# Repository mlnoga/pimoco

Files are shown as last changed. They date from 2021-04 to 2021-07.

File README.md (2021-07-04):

# pimoco

Telescope mount and focuser control with a Raspberry Pi 

Assembled PCB

## Motivation

Why do we need a separate device to control stepper motors attached to a telescope? Often times, a Raspberry Pi 4 running Ekos/Kstars/Indi will be attached to the telescope anyway, providing plenty of compute power. Modern stepper motor controllers like the Trinamic TMC5160 have an on-board motion controller which accepts position read, set target speed and go-to commands via SPI. The Raspberry Pi has two such interfaces for a total of five devices on its GPIO port.

This is 
* capable (1/256 microsteps, up to 1000x sidereal slewing, silent tracking, load-adaptive speed w/o step loss)
* robust (no Wifi, Bluetooth or USB connections to the mount as a source of error)
* beautiful (supports SkySafari on phones/tablets and game controllers via Ekos/Kstars/Indi) 
* inexpensive (no need for separate microcontrollers like OnStep or TeenAstro)
* manageable (no separate device firmware, only Indi drivers which Linux package managers can update)     

## [Wiki](../../wiki)

* [Hardware](../../wiki/Hardware)
* [Software](../../wiki/Software)
* [Results](../../wiki/Results)

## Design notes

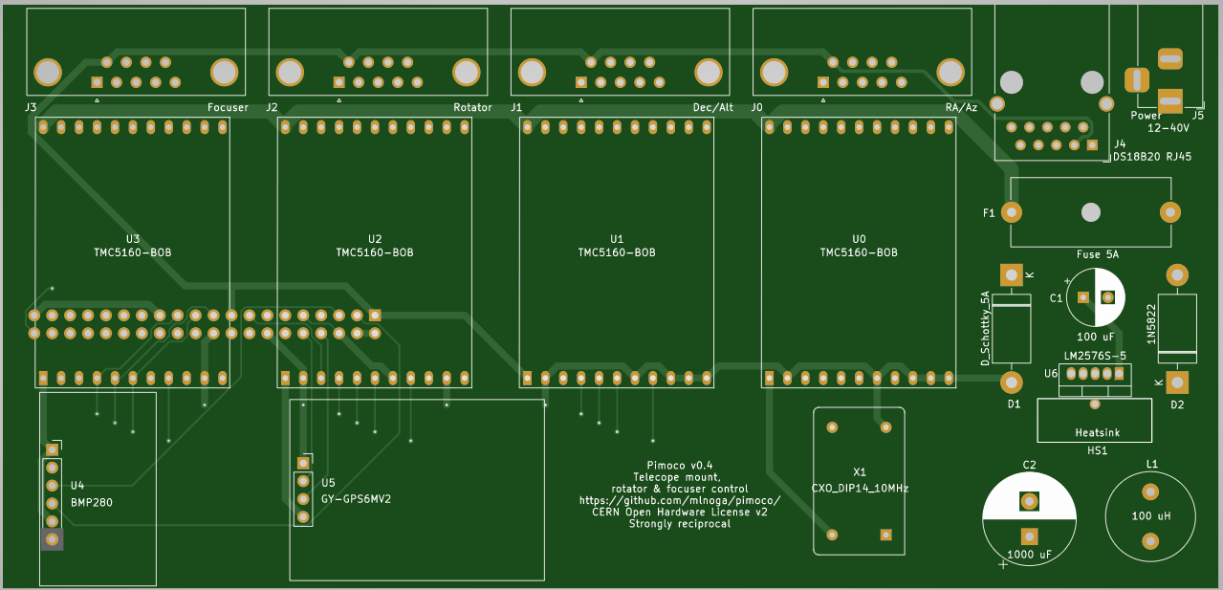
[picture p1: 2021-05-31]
hardware/images/top-v0.4.png

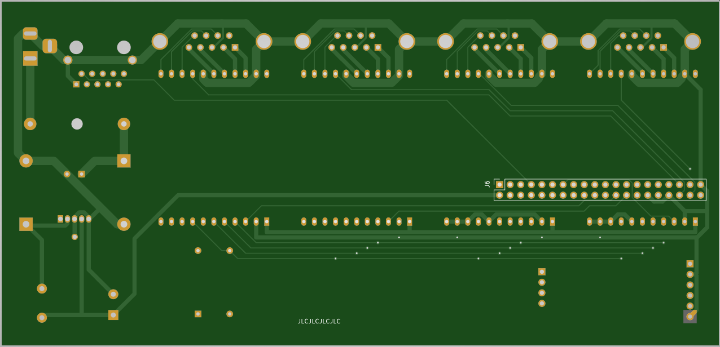
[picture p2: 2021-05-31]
hardware/images/bottom-v0.4.png

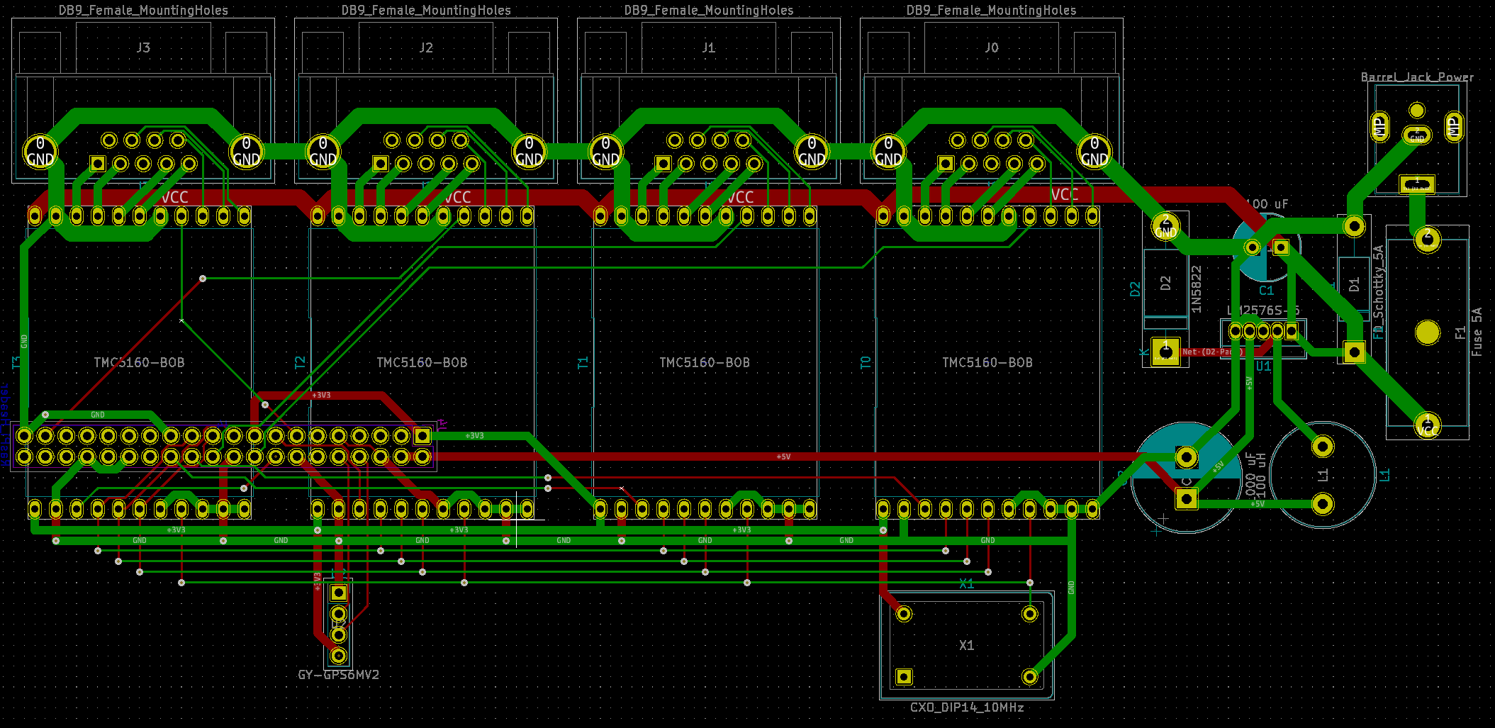
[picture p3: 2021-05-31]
hardware/images/platinenlayout.png

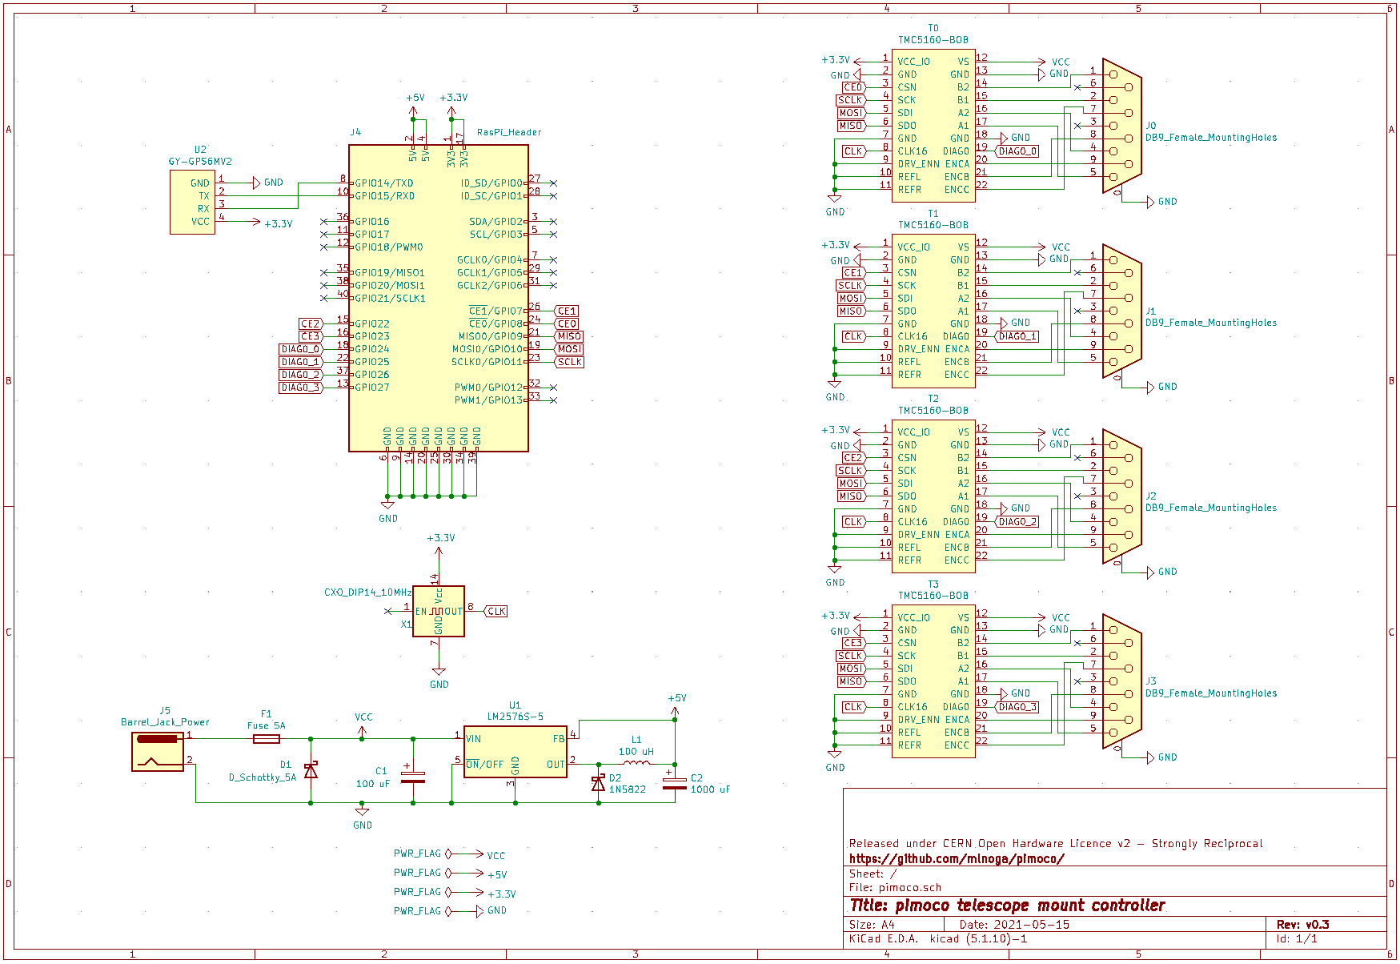
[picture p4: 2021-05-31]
hardware/images/schaltplan.png

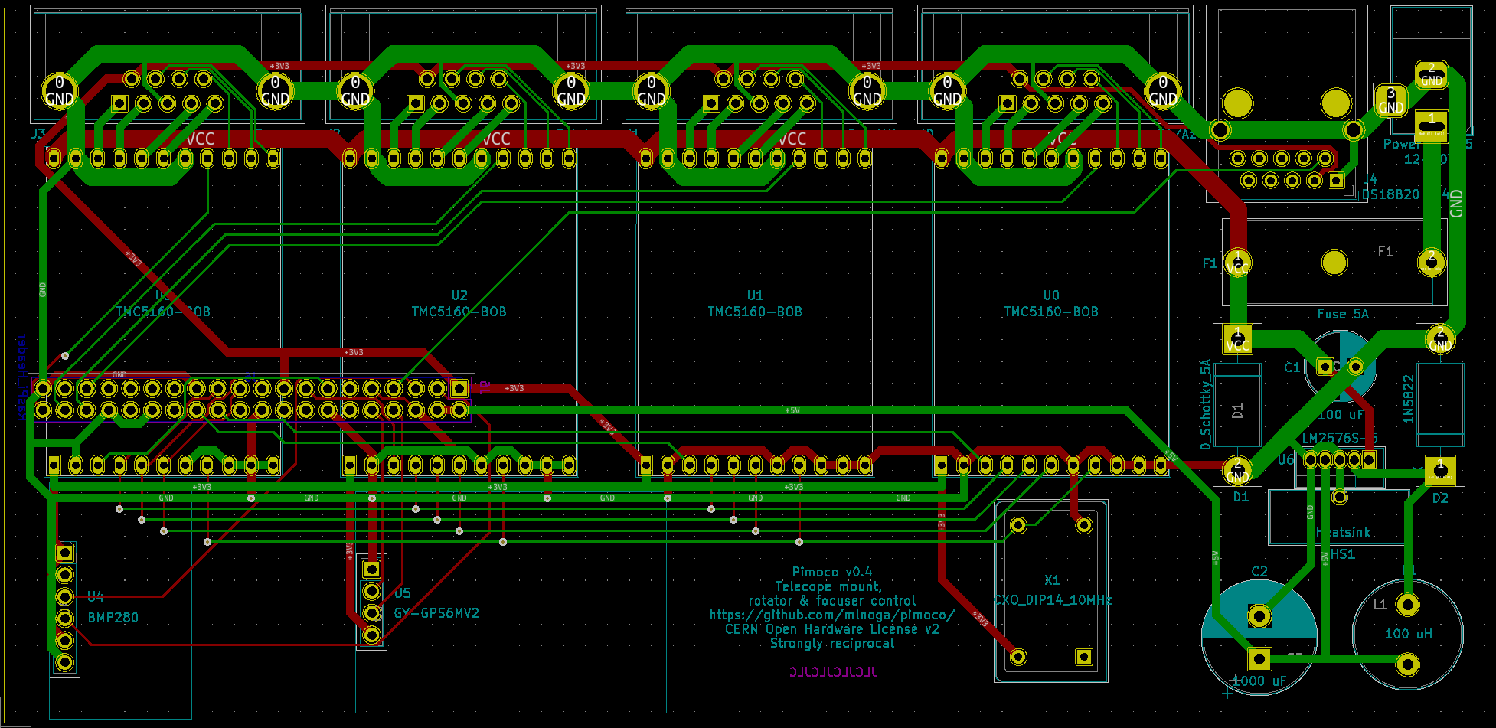
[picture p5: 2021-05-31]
hardware/images/layout-v0.4.png

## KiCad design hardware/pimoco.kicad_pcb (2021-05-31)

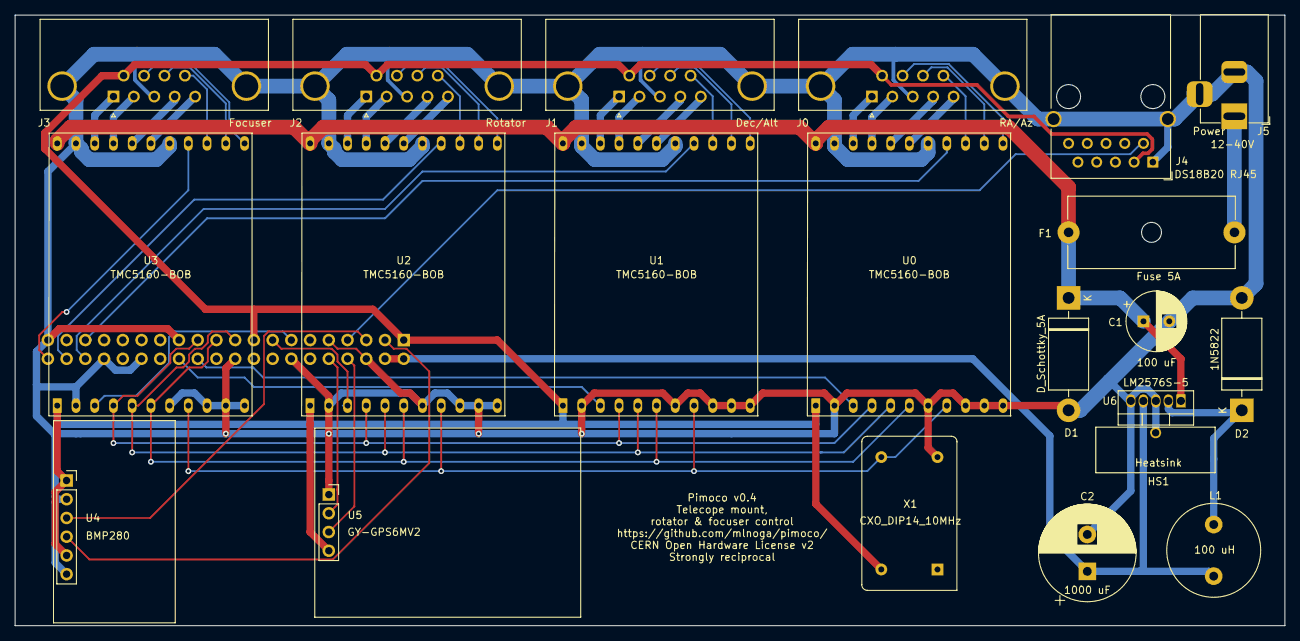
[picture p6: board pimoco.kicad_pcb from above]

Board: 2 copper layers, 172.2 x 82.8 mm, 22 parts (1 on the bottom side), 51 nets.

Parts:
C1: 100 uF; CP_Radial_D8.0mm_P3.50mm
C2: 1000 uF; CP_Radial_D13.0mm_P5.00mm
D1: D_Schottky_5A; D_DO-201AD_P15.24mm_Horizontal
D2: 1N5822; D_DO-201AD_P15.24mm_Horizontal
F1: Fuse 5A; Fuseholder_Cylinder-5x20mm_Schurter_0031_8201_Horizontal_Op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
HS1: Heatsink; Heatsink_TO-220_vertical
J0: RA/Az; DSUB-9_Female_Horizontal_P2.77x2.84mm_EdgePinOffset7.70mm_H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
J1: Dec/Alt; DSUB-9_Female_Horizontal_P2.77x2.84mm_EdgePinOffset7.70mm_H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
J2: Rotator; DSUB-9_Female_Horizontal_P2.77x2.84mm_EdgePinOffset7.70mm_H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
J3: Focuser; DSUB-9_Female_Horizontal_P2.77x2.84mm_EdgePinOffset7.70mm_H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
J4: DS18B20 RJ45; RJ45_Wuerth_7499111446_Horizontal-modified
J5: Power; BarrelJack_Horizontal
J6: RasPi_Header; PinSocket_2x20_P2.54mm_Vertical
L1: 100 uH; L_Radial_D12.5mm_P7.00mm_Fastron_09HCP
U0, U1, U2, U3: TMC5160-BOB; TMC5160-BOB2
U4: BMP280; BMP280-Breakout
U5: GY-GPS6MV2
U6: LM2576S-5; TO-220-5_Vertical
X1: CXO_DIP14_10MHz; Oscillator_DIP-14

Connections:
+3V3: J0.6, J1.6, J2.6, J3.6, J4.3, J6.1, J6.17, U0.1, U1.1, U2.1, U3.1, U4.1, U4.5, U5.4, X1.14
+5V: C2.1, J6.2, J6.4, L1.2, U6.4
CE0: J6.24, U0.3
CE1: J6.26, U1.3
CE2: J6.15, U2.3
CE3: J6.13, U3.3
CLK: U0.8, U1.8, U2.8, U3.8, X1.8
DIAG0_0: J6.35, U0.19
DIAG0_1: J6.36, U1.19
DIAG0_2: J6.38, U2.19
DIAG0_3: J6.40, U3.19
GND: C1.2, C2.2, D1.2, D2.2, HS1.1, J0.0, J0.3, J1.0, J1.3, J2.0, J2.3, J3.0, J3.3, J4.1, J4.SH, J5.2, J5.3, J6.6, J6.9, J6.14, J6.20, J6.25, J6.30, J6.34, J6.39, U0.2, U0.7, U0.9, U0.10, U0.11, U0.13, U0.18, U1.2, U1.7, U1.9, U1.10, U1.11, U1.13, U1.18, U2.2, U2.7, U2.9, U2.10, U2.11, U2.13, U2.18, U3.2, U3.7, U3.9, U3.10, U3.11, U3.13, U3.18, U4.2, U4.6, U5.1, U6.3, U6.5, X1.7
MISO: J6.21, U0.6, U1.6, U2.6, U3.6
MOSI: J6.19, U0.5, U1.5, U2.5, U3.5
unnamed: D2.1, L1.1, U6.2
unnamed: F1.2, J5.1
unnamed: J0.1, U0.14
unnamed: J0.2, U0.15
unnamed: J0.4, U0.16
unnamed: J0.5, U0.17
unnamed: J0.7, U0.22
unnamed: J0.8, U0.21
unnamed: J0.9, U0.20
unnamed: J1.1, U1.14
unnamed: J1.2, U1.15
unnamed: J1.4, U1.16
unnamed: J1.5, U1.17
unnamed: J1.7, U1.22
unnamed: J1.8, U1.21
unnamed: J1.9, U1.20
unnamed: J2.1, U2.14
unnamed: J2.2, U2.15
unnamed: J2.4, U2.16
unnamed: J2.5, U2.17
unnamed: J2.7, U2.22
unnamed: J2.8, U2.21
unnamed: J2.9, U2.20
unnamed: J3.1, U3.14
unnamed: J3.2, U3.15
unnamed: J3.4, U3.16
unnamed: J3.5, U3.17
unnamed: J3.7, U3.22
unnamed: J3.8, U3.21
unnamed: J3.9, U3.20
unnamed: J4.2, J6.7
unnamed: J6.3, U4.4
unnamed: J6.5, U4.3
unnamed: J6.8, U5.3
unnamed: J6.10, U5.2
SCLK: J6.23, U0.4, U1.4, U2.4, U3.4
VCC: C1.1, D1.1, F1.1, U0.12, U1.12, U2.12, U3.12, U6.1

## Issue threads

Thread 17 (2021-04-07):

Enhance motor control with SpreadChop/FullStep/StallGuard etc.

mlnoga, 2021-04-07:

Closed 2021-04-28.

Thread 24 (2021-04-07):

Add support for meridian flip to mount

mlnoga, 2021-04-07:

Closed 2021-05-09.

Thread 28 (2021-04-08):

Add 5V 3A voltage regulator to breadboard to power the pi w/o separate PSU

mlnoga, 2021-04-08:

mlnoga, 2021-04-28:
E.g. the [LM2576](https://www.ti.com/lit/ds/symlink/lm2576.pdf)

mlnoga, 2021-05-05:
Successful. See [wiki](https://github.com/mlnoga/pimoco/wiki/Hardware)

Closed 2021-05-05.

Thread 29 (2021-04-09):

Set gpclk0 with wiringPi to remove need for an /etc/rc.local entry

mlnoga, 2021-04-09:

mlnoga, 2021-04-24:
GPCLK0 rates are different on Pi4 than Pi3 by a factor of approx. 3x. Exact base clocks are undocumented in the Broadcom CPU reference. Abandoning this approach and moving to external 10 MHz crystal oscillator.

Closed 2021-04-24.

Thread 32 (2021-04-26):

Gotos dont consistently signal completion.

mlnoga, 2021-04-26:
Gotos dont consistently signal completion.

mlnoga, 2021-05-12:
The underlying issue seems to be that the TMC5160 really does need SPI mode 3, which is broken on RPI SPI1 and SPI2.

So far I've used [Raspberry Pi SPI ](https://www.raspberrypi.org/documentation/hardware/raspberrypi/spi/README.md) port 1, because it supports three CS lines for the three steppers. This keeps MISO/MOSI/Clock wiring to a minimum. I've had initial success, but not full stability, with mode 0. Here's the `dmesg` kernel log entry when trying to set mode 3:

```
spidev spi1.0: setup: unsupported mode bits 1
```

So the Broadcom chipset for the two so-called "mini" SPI ports 1 and 2 appears to be broken. According to these sources, it only supports modes 0 and 2:

* [Stackexchange](https://raspberrypi.stackexchange.com/questions/106456/cant-set-modes-1-and-3-in-auxillary-spi1)
* [Raspberry Pi Forum](https://www.raspberrypi.org/forums/viewtopic.php?p=1071641)

The fix appears to be to use the full SPI port 0 with two CS lines, and another of the new SPI ports 3-6 available on RPi4. With header pin numbers, available ports are:

| Line    | SPI0  | SPI3 | SPI4 | SPI 5 | SPI6 |
|--------|-------|------|------|-------|------|
| MOSI  |   19   |    3   |  31  |     8   |   38   |
| MISO  |    21  |   28  |  29  |   33   |   35   |
| SCLK  |     23  |     5  |  26  |   10   |   40   |
| CE0    |     24  |   27  |  07  |   32   |   12   |
| CE1    |     26  |   18  |  22  |   37   |   13   |

So hardware change required, and restriction to RPI4 and above when needing three or more SPI ports.

mlnoga, 2021-05-12:
Looks like SPI0 and SPI3 are the way to go.

[Device tree README](https://github.com/raspberrypi/firmware/blob/master/boot/overlays/README)

mlnoga, 2021-05-24:
SPI0 with CS0, CS1, CS2, CS3 is the way to go.

mlnoga, 2021-05-25:
Another issue is HA endlessly chasing the target position at low speeds due to target resets

Closed 2021-05-25.

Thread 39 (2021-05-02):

When mount limits disable tracking, it doesn't automatically reenable once the mount is back within limits

mlnoga, 2021-05-02:

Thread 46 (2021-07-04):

Telescope driver crashes after motor initialization with new PCB

mlnoga, 2021-07-04:
Logfile

```
[2021-07-04T12:06:55.642 CEST DEBG ][                org.kde.kstars] - Daylight Saving Time active
[2021-07-04T12:06:55.643 CEST DEBG ][                org.kde.kstars] - Next Daylight Savings Time change (Local Time):  "Sun Oct 31 00:59:59 2021 GMT"
[2021-07-04T12:06:55.643 CEST DEBG ][                org.kde.kstars] - Next Daylight Savings Time change (UTC):  "Sat Oct 30 22:59:59 2021 GMT"
[2021-07-04T12:06:55.643 CEST DEBG ][                org.kde.kstars] - Starting the timer
[2021-07-04T12:06:55.962 CEST DEBG ][           org.kde.kstars.ekos] - Resetting Ekos Manager...
[2021-07-04T12:06:56.032 CEST INFO ][           org.kde.kstars.ekos] - "Starting INDI services..."
[2021-07-04T12:06:56.033 CEST DEBG ][           org.kde.kstars.indi] - INDI: Starting local drivers...
[2021-07-04T12:06:56.034 CEST DEBG ][           org.kde.kstars.indi] - Starting INDI Server:  ("-v", "-p", "7624", "-m", "1024", "-r", "0", "-f", "/tmp/indififo039d8cfc") -f "/tmp/indififo039d8cfc"
[2021-07-04T12:06:56.051 CEST DEBG ][           org.kde.kstars.indi] - INDI Server Started?  true
[2021-07-04T12:06:56.052 CEST DEBG ][           org.kde.kstars.indi] - INDI: INDI Server started locally on port  7624
[2021-07-04T12:06:56.052 CEST DEBG ][           org.kde.kstars.indi] - Starting INDI Driver  "indi_pimoco_mount"
[2021-07-04T12:06:56.053 CEST DEBG ][           org.kde.kstars.indi] - Starting INDI Driver  "indi_asi_ccd"
[2021-07-04T12:06:56.053 CEST DEBG ][           org.kde.kstars.indi] - Starting INDI Driver  "indi_asi_wheel"
[2021-07-04T12:06:56.053 CEST DEBG ][           org.kde.kstars.indi] - Starting INDI Driver  "indi_pimoco_focuser"
[2021-07-04T12:06:56.054 CEST DEBG ][           org.kde.kstars.indi] - Starting INDI Driver  "indi_joystick"
[2021-07-04T12:06:56.054 CEST DEBG ][           org.kde.kstars.indi] - Starting INDI Driver  "indi_skysafari"
[2021-07-04T12:06:56.054 CEST DEBG ][           org.kde.kstars.indi] - Adding managed driver "Pimoco mount"
[2021-07-04T12:06:56.054 CEST DEBG ][           org.kde.kstars.indi] - Adding managed driver "ZWO CCD"
[2021-07-04T12:06:56.054 CEST DEBG ][           org.kde.kstars.indi] - Adding managed driver "ASI EFW"
[2021-07-04T12:06:56.055 CEST DEBG ][           org.kde.kstars.indi] - Adding managed driver "Pimoco focuser"
[2021-07-04T12:06:56.055 CEST DEBG ][           org.kde.kstars.indi] - Adding managed driver "Joystick"
[2021-07-04T12:06:56.055 CEST DEBG ][           org.kde.kstars.indi] - Adding managed driver "SkySafari"
[2021-07-04T12:06:56.057 CEST DEBG ][           org.kde.kstars.indi] - INDIListener: Adding a new client manager to INDI listener..
[2021-07-04T12:06:56.057 CEST DEBG ][           org.kde.kstars.indi] - INDI: Connecting to local INDI server on port  7624  ...
[2021-07-04T12:06:56.059 CEST DEBG ][           org.kde.kstars.indi] - Connection to INDI server is successful
[2021-07-04T12:06:56.060 CEST INFO ][           org.kde.kstars.ekos] - "INDI services started on port 7624."
[2021-07-04T12:06:56.072 CEST DEBG ][           org.kde.kstars.indi] - INDI server connected.
[2021-07-04T12:06:56.135 CEST DEBG ][           org.kde.kstars.indi] - Received new device Pimoco focuser
[2021-07-04T12:06:56.157 CEST DEBG ][           org.kde.kstars.indi] - INDI Server:  "2021-07-04T10:06:56: startup: /usr/bin/indiserver -v -p 7624 -m 1024 -r 0 -f /tmp/indififo039d8cfc "
[2021-07-04T12:06:56.158 CEST DEBG ][           org.kde.kstars.indi] - INDI Server:  "2021-07-04T10:06:56: listening to port 7624 on fd 3"
[2021-07-04T12:06:56.158 CEST DEBG ][           org.kde.kstars.indi] - INDI Server:  "FIFO: start indi_pimoco_mount -n \"Pimoco mount\""
[2021-07-04T12:06:56.158 CEST DEBG ][           org.kde.kstars.indi] - INDI Server:  "With name: Pimoco mount"
[2021-07-04T12:06:56.158 CEST DEBG ][           org.kde.kstars.indi] - INDI Server:  "FIFO: Starting driver indi_pimoco_mount"
[2021-07-04T12:06:56.159 CEST DEBG ][           org.kde.kstars.indi] - INDI Server:  "2021-07-04T10:06:56: Driver indi_pimoco_mount: pid=2469 rfd=4 wfd=7 efd=8"
[2021-07-04T12:06:56.159 CEST DEBG ][           org.kde.kstars.indi] - INDI Server:  "FIFO: start indi_asi_ccd"
[2021-07-04T12:06:56.159 CEST DEBG ][           org.kde.kstars.indi] - INDI Server:  "FIFO: Starting driver indi_asi_ccd"
[2021-07-04T12:06:56.159 CEST DEBG ][           org.kde.kstars.indi] - INDI Server:  "2021-07-04T10:06:56: Driver indi_asi_ccd: pid=2470 rfd=5 wfd=10 efd=11"
[2021-07-04T12:06:56.159 CEST DEBG ][           org.kde.kstars.indi] - INDI Server:  "FIFO: start indi_asi_wheel"
[2021-07-04T12:06:56.160 CEST DEBG ][           org.kde.kstars.indi] - INDI Server:  "FIFO: Starting driver indi_asi_wheel"
[2021-07-04T12:06:56.160 CEST DEBG ][           org.kde.kstars.indi] - INDI Server:  "2021-07-04T10:06:56: Driver indi_asi_wheel: pid=2471 rfd=6 wfd=15 efd=16"
[2021-07-04T12:06:56.160 CEST DEBG ][           org.kde.kstars.indi] - INDI Server:  "FIFO: start indi_pimoco_focuser -n \"Pimoco focuser\""
[2021-07-04T12:06:56.160 CEST DEBG ][           org.kde.kstars.indi] - INDI Server:  "With name: Pimoco focuser"
[2021-07-04T12:06:56.160 CEST DEBG ][           org.kde.kstars.indi] - INDI Server:  "FIFO: Starting driver indi_pimoco_focuser"
[2021-07-04T12:06:56.161 CEST DEBG ][           org.kde.kstars.indi] - INDI Server:  "2021-07-04T10:06:56: Driver indi_pimoco_focuser: pid=2472 rfd=9 wfd=18 efd=19"
[2021-07-04T12:06:56.161 CEST DEBG ][           org.kde.kstars.indi] - INDI Server:  "FIFO: start indi_joystick -n \"Joystick\""
[2021-07-04T12:06:56.161 CEST DEBG ][           org.kde.kstars.indi] - INDI Server:  "With name: Joystick"
[2021-07-04T12:06:56.161 CEST DEBG ][           org.kde.kstars.indi] - INDI Server:  "FIFO: Starting driver indi_joystick"
[2021-07-04T12:06:56.161 CEST DEBG ][           org.kde.kstars.indi] - INDI Server:  "2021-07-04T10:06:56: Driver indi_joystick: pid=2473 rfd=12 wfd=21 efd=22"
[2021-07-04T12:06:56.162 CEST DEBG ][           org.kde.kstars.indi] - INDI Server:  "FIFO: start indi_skysafari -n \"SkySafari\""
[2021-07-04T12:06:56.162 CEST DEBG ][           org.kde.kstars.indi] - INDI Server:  "With name: SkySafari"
[2021-07-04T12:06:56.162 CEST DEBG ][           org.kde.kstars.indi] - INDI Server:  "FIFO: Starting driver indi_skysafari"
[2021-07-04T12:06:56.162 CEST DEBG ][           org.kde.kstars.indi] - INDI Server:  "2021-07-04T10:06:56: Driver indi_skysafari: pid=2474 rfd=17 wfd=24 efd=25"
[2021-07-04T12:06:56.162 CEST DEBG ][           org.kde.kstars.indi] - INDI Server:  "2021-07-04T10:06:56: Client 20: new arrival from 127.0.0.1:41234 - welcome!"
[2021-07-04T12:06:56.163 CEST DEBG ][           org.kde.kstars.indi] - INDI Server:  "2021-07-04T10:06:56: Driver indi_pimoco_mount: snooping on GPS Simulator.GEOGRAPHIC_COORD"
[2021-07-04T12:06:56.163 CEST DEBG ][           org.kde.kstars.indi] - INDI Server:  "2021-07-04T10:06:56: Driver indi_pimoco_mount: snooping on GPS Simulator.TIME_UTC"
[2021-07-04T12:06:56.163 CEST DEBG ][           org.kde.kstars.indi] - INDI Server:  "2021-07-04T10:06:56: Driver indi_pimoco_mount: snooping on Dome Simulator.DOME_PARK"
[2021-07-04T12:06:56.163 CEST DEBG ][           org.kde.kstars.indi] - INDI Server:  "2021-07-04T10:06:56: Driver indi_pimoco_mount: snooping on Dome Simulator.DOME_SHUTTER"
[2021-07-04T12:06:56.164 CEST DEBG ][           org.kde.kstars.indi] - INDI Server:  "2021-07-04T10:06:56: Driver indi_asi_wheel: Searching for HID Device VID: 0x3c3 PID: 0x1f01"
[2021-07-04T12:06:56.164 CEST DEBG ][           org.kde.kstars.indi] - INDI Server:  ""
[2021-07-04T12:06:56.208 CEST DEBG ][           org.kde.kstars.indi] - INDIListener: New device "Pimoco focuser"
[2021-07-04T12:06:56.208 CEST INFO ][           org.kde.kstars.ekos] - Ekos received a new device:  "Pimoco focuser"
[2021-07-04T12:06:56.214 CEST DEBG ][           org.kde.kstars.indi] - Received new device Pimoco mount
[2021-07-04T12:06:56.215 CEST DEBG ][           org.kde.kstars.indi] - INDI Server:  "2021-07-04T10:06:56: Driver indi_asi_wheel: Searching for HID Device VID: 0x3c3 PID: 0x1f02"
[2021-07-04T12:06:56.216 CEST DEBG ][           org.kde.kstars.indi] - INDI Server:  "2021-07-04T10:06:56: Driver indi_asi_wheel: No ASI EFW detected.Searching for HID Device VID: 0x3c3 PID: 0x1f01"
[2021-07-04T12:06:56.216 CEST DEBG ][           org.kde.kstars.indi] - INDI Server:  "2021-07-04T10:06:56: Driver indi_asi_wheel: Searching for HID Device VID: 0x3c3 PID: 0x1f02"
[2021-07-04T12:06:56.217 CEST DEBG ][           org.kde.kstars.indi] - INDI Server:  ""
[2021-07-04T12:06:56.358 CEST DEBG ][           org.kde.kstars.indi] - INDIListener: New device "Pimoco mount"
[2021-07-04T12:06:56.359 CEST INFO ][           org.kde.kstars.ekos] - Ekos received a new device:  "Pimoco mount"
[2021-07-04T12:06:56.366 CEST DEBG ][           org.kde.kstars.indi] - Received new device SkySafari
[2021-07-04T12:06:56.501 CEST DEBG ][           org.kde.kstars.indi] - INDI Server:  "2021-07-04T10:06:56: Client 23: new arrival from 127.0.0.1:41236 - welcome!"
[2021-07-04T12:06:56.502 CEST DEBG ][           org.kde.kstars.indi] - INDI Server:  "2021-07-04T10:06:56: Driver indi_asi_wheel: No ASI EFW detected.Searching for HID Device VID: 0x3c3 PID: 0x1f01"
[2021-07-04T12:06:56.503 CEST DEBG ][           org.kde.kstars.indi] - INDI Server:  "2021-07-04T10:06:56: Driver indi_asi_wheel: Searching for HID Device VID: 0x3c3 PID: 0x1f02"
[2021-07-04T12:06:56.503 CEST DEBG ][           org.kde.kstars.indi] - INDI Server:  ""
[2021-07-04T12:06:56.510 CEST DEBG ][           org.kde.kstars.indi] - < Pimoco mount >: < CONNECTION >
[2021-07-04T12:06:56.513 CEST DEBG ][           org.kde.kstars.indi] - < Pimoco mount >: < DRIVER_INFO >
[2021-07-04T12:06:56.521 CEST DEBG ][           org.kde.kstars.indi] - < Pimoco mount >: < POLLING_PERIOD >
[2021-07-04T12:06:56.524 CEST DEBG ][           org.kde.kstars.indi] - < Pimoco mount >: < DEBUG >
[2021-07-04T12:06:56.527 CEST DEBG ][           org.kde.kstars.indi] - < Pimoco mount >: < CONFIG_PROCESS >
[2021-07-04T12:06:56.529 CEST DEBG ][           org.kde.kstars.indi] - < Pimoco focuser >: < CONNECTION >
[2021-07-04T12:06:56.533 CEST DEBG ][           org.kde.kstars.indi] - < Pimoco focuser >: < DRIVER_INFO >
[2021-07-04T12:06:56.541 CEST DEBG ][           org.kde.kstars.indi] - < Pimoco focuser >: < DEBUG >
[2021-07-04T12:06:56.544 CEST DEBG ][           org.kde.kstars.indi] - < Pimoco focuser >: < POLLING_PERIOD >
[2021-07-04T12:06:56.551 CEST DEBG ][           org.kde.kstars.indi] - < Pimoco focuser >: < CONFIG_PROCESS >
[2021-07-04T12:06:56.555 CEST INFO ][           org.kde.kstars.indi] - Pimoco focuser :  "[INFO] Debug is enabled. "
[2021-07-04T12:06:56.555 CEST DEBG ][           org.kde.kstars.indi] - < Pimoco focuser >: < DEBUG_LEVEL >
[2021-07-04T12:06:56.557 CEST DEBG ][           org.kde.kstars.indi] - < Pimoco focuser >: < LOGGING_LEVEL >
[2021-07-04T12:06:56.559 CEST DEBG ][           org.kde.kstars.indi] - < Pimoco focuser >: < LOG_OUTPUT >
[2021-07-04T12:06:56.561 CEST DEBG ][           org.kde.kstars.indi] - Pimoco focuser : "[DEBUG] Toggle Debug Level -- Driver Debug "
[2021-07-04T12:06:56.561 CEST DEBG ][           org.kde.kstars.indi] - Pimoco focuser : "[DEBUG] Toggle Logging Level -- Messages "
[2021-07-04T12:06:56.571 CEST DEBG ][           org.kde.kstars.indi] - INDIListener: New device "SkySafari"
[2021-07-04T12:06:56.572 CEST INFO ][           org.kde.kstars.ekos] - Ekos received a new device:  "SkySafari"
[2021-07-04T12:06:56.573 CEST DEBG ][           org.kde.kstars.indi] - Received new device Joystick
[2021-07-04T12:06:56.599 CEST DEBG ][           org.kde.kstars.indi] - < SkySafari >: < CONNECTION >
[2021-07-04T12:06:56.604 CEST DEBG ][           org.kde.kstars.indi] - < SkySafari >: < DRIVER_INFO >
[2021-07-04T12:06:56.619 CEST DEBG ][           org.kde.kstars.indi] - < SkySafari >: < DEBUG >
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

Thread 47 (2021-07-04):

Fix minor hardware issues in PCB v0.4

mlnoga, 2021-07-04:
- Make drill hole for heat sink 0.3mm wider
- Move GPS connector pin left towards BMP sensor to leave more room for the GPS antenna
- Move RPi connector header down away from connector edge to make connectors flush with the connectors on the RPI itself

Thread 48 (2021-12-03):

I think the .lib file is missing from the hardware folder

skieast, 2021-12-03:
I was trying to look at the schematic in KiCad and the symbols aren't defined.
Thanks

Closed 2021-12-04.

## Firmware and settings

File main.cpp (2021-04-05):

/*
    PiMoCo: Raspberry Pi Telescope Mount and Focuser Control
    Copyright (C) 2021 Markus Noga

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
    You should have received a copy of the GNU General Public License
    along with this program.  If not, see <https://www.gnu.org/licenses/>.
*/


#include <stdio.h>
#include <stdarg.h>
#include <stdlib.h>
#include <locale.h> // for thousands separator
#include <unistd.h> // for sleep
#include <libindi/indifocuser.h>

#include "pimoco_stepper.h"

// Unused dummies for Indi functions to avoid linker errors
//
extern "C" {

void ISGetProperties(const char *dev) {}

void ISNewBLOB(const char *dev, const char *name, int sizes[], int blobsizes[], char *blobs[], char *formats[], char *names[], int n) {}

void ISNewNumber(const char *dev, const char *name, double values[], char *names[], int n) {}

void ISNewSwitch(const char *dev, const char *name, ISState *states, char *names[], int n) {}

void ISNewText(const char *dev, const char *name, char *texts[], char *names[], int n) {}

void ISSnoopDevice(XMLEle *root) {}

} // extern "C"


void panicf(const char *fmt, ...) {
	va_list argp;
	va_start(argp, fmt);
	vfprintf(stdout, fmt, argp);
	exit(-1);
}

void getAndPrintState(Stepper *stepper) {
	int32_t pos, speed;
	if(!stepper->getPosition(&pos) || !stepper->getSpeed(&speed))
		panicf("Error getting position and speed\n");

	printf("Current position is %'+d; speed is %'+d and status is ", pos, speed);
	const int bufsize=1023;
	char buffer[bufsize+1]={0};
	TMC5160::printStatus(buffer, bufsize, stepper->getStatus());
	puts(buffer);
}

int main(int argc, char ** argv) {
	puts("Starting up...");

	setlocale(LC_ALL, ""); // for thousands separator
	Stepper stepper("Default stepper");

	if(!stepper.open(Stepper::defaultSPIDevice))
		panicf("Error opening device %s\n", Stepper::defaultSPIDevice);

	getAndPrintState(&stepper);

	if(!stepper.syncPosition(0))
		panicf("Error syncing position\n");

	getAndPrintState(&stepper);

	uint32_t fullRevolutionInUsteps=256ul*400*3*144;
	// move by 1h of RA with 256 microsteps, 400 steps/rev, belt ratio 1:3 and Vixen worm gear ratio 1:144  
	if(!stepper.setTargetPositionBlocking((fullRevolutionInUsteps*1ul)/24))  
		panicf("Error on goto");

	getAndPrintState(&stepper);

	if(!stepper.setTargetPositionBlocking(0))
		panicf("Error on goto");
	
	getAndPrintState(&stepper);

	// WiringPi uses crystal osciallator running at 19.2 MHz for void gpioClockSet (int pin, int freq). 
	// See https://github.com/WiringPi/WiringPi/blob/master/wiringPi/wiringPi.c
	// TMC5160 needs 8..10-16 MHz, see section 26.2.1 in https://www.trinamic.com/fileadmin/assets/Products/ICs_Documents/TMC5160A_Datasheet_Rev1.14.pdf 
	// To have an exact frequency based on an integer divider of two, we choose 9.6 MHz.
	double stepperClockInHz=9600000;  
	double stepperChipTimeScaler=(double) (1ul<<24);
	double stepperTimeUnit=stepperChipTimeScaler/stepperClockInHz;

	double siderealDayInSeconds=86164.0905;

	double siderealRateInUstepsPerTimeUnit=(((double)fullRevolutionInUsteps)/siderealDayInSeconds)*stepperTimeUnit;
	uint32_t siderealRateInUstepsPerTimeUnitRounded=(uint32_t) (siderealRateInUstepsPerTimeUnit+0.5);
	if(!stepper.setTargetSpeed(siderealRateInUstepsPerTimeUnitRounded))
		panicf("Error on setSpeed");

	for(int i=0; i<60; i++) {
		sleep(1);
		getAndPrintState(&stepper);
	}

	if(!stepper.setTargetSpeed(0))
		panicf("Error on setSpeed");
	getAndPrintState(&stepper);
	sleep(1);
	getAndPrintState(&stepper);

	if(!stepper.setTargetPositionBlocking(0))
		panicf("Error on goto");
	
	getAndPrintState(&stepper);

	puts("Exiting...");
	return 0;
}

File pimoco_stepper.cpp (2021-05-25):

/*
    PiMoCo: Raspberry Pi Telescope Mount and Focuser Control
    Copyright (C) 2021 Markus Noga

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
    You should have received a copy of the GNU General Public License
    along with this program.  If not, see <https://www.gnu.org/licenses/>.
*/


#include <unistd.h>
#include <fcntl.h>
#include <sys/stat.h>
#include <sys/ioctl.h>
#include <linux/types.h>
#include <linux/spi/spidev.h>
#include <cstdio>
#include <math.h> // for round(), M_PI
#include <sys/time.h>  // for gettimeofday() etc.
#include <libindi/indilogger.h> // for LOG_..., LOGF_... macros
#include <wiringPi.h> // for GPIO etc

#include "pimoco_stepper.h"
#include "pimoco_time.h"


const uint32_t Stepper::defaultHardwareMaxCurrent_mA=3100; // default for TMC5160-BOB
const int32_t  Stepper::defaultMinPosition=-1000ul*1000ul*256ul;
const int32_t  Stepper::defaultMaxPosition= 1000ul*1000ul*256ul;
const int32_t  Stepper::defaultMaxGoToSpeed=100000;
const double   Stepper::defaultStepsPerRev =400;
const double   Stepper::defaultGearRatio   =3*144;


Stepper::Stepper(const char *theIndiDeviceName, const char *theAxisName, int diag0Pin)
					 : TMC5160(theIndiDeviceName, theAxisName, diag0Pin), 
					 minPosition(defaultMinPosition), maxPosition(defaultMaxPosition),
				     maxGoToSpeed(defaultMaxGoToSpeed), hardwareMaxCurrent_mA(defaultHardwareMaxCurrent_mA),
				     stepsPerRev(defaultStepsPerRev), gearRatio(defaultGearRatio) {
}


Stepper::~Stepper() {
	stop();
}

bool Stepper::open(const char *deviceName) {
	if(!TMC5160::open(deviceName))
		return false;

	if((!Handshake()) || (!Init())) {
		TMC5160::close();
		return false;
	}

	return true;
}


bool Stepper::Handshake() {
	// try sending test pattern and capturing response
	const uint32_t len=5*5;
	uint8_t tx[len]={
		TMCR_X_ENC | 0x80, 0x01, 0x02, 0x03, 0x04,  // set XENC to 0x01020304
		TMCR_X_ENC       , 0x11, 0x12, 0x13, 0x14,  // get XENC
		TMCR_X_ENC | 0x80, 0x21, 0x22, 0x23, 0x24,  // set XENC to 0x21222324
		TMCR_X_ENC       , 0x31, 0x32, 0x33, 0x34,  // get XENC
		TMCR_X_ENC       , 0x41, 0x42, 0x43, 0x44,  // get XENC
	};
	uint8_t rx[len];
	if(!sendReceive(tx, rx, len)) {
		LOGF_WARN("%s: Handshake failed: send/receive", getAxisName());
		return false;
	}

	if(debugLevel>=TMC_DEBUG_DEBUG)
		for(uint32_t i=0; i<5; i++)
			LOGF_DEBUG("%d: sent %02x %02x %02x %02x %02x   recv %02x %02x %02x %02x %02x", i, tx[5*i+0], tx[5*i+1], tx[5*i+2], tx[5*i+3], tx[5*i+4],  rx[5*i+0], rx[5*i+1], rx[5*i+2], rx[5*i+3], rx[5*i+4]  );

	// validate responses
	if(rx[5*1+1]!=tx[5*0+1] || rx[5*1+2]!=tx[5*0+2] || rx[5*1+3]!=tx[5*0+3] || rx[5*1+4]!=tx[5*0+4] ) {
		LOGF_WARN("%s: Handshake failed: got %02x %02x %02x %02x after first set", getAxisName(), rx[5*1+1], rx[5*1+2], rx[5*1+3], rx[5*1+4]);
		return false;
	}
	if(rx[5*2+1]!=tx[5*0+1] || rx[5*2+2]!=tx[5*0+2] || rx[5*2+3]!=tx[5*0+3] || rx[5*2+4]!=tx[5*0+4] ) {
		LOGF_WARN("%s: Handshake failed: got %02x %02x %02x %02x after first get", getAxisName(), rx[5*2+1], rx[5*2+2], rx[5*2+3], rx[5*2+4]);
		return false;
	}
	if(rx[5*3+1]!=tx[5*2+1] || rx[5*3+2]!=tx[5*2+2] || rx[5*3+3]!=tx[5*2+3] || rx[5*3+4]!=tx[5*2+4] ) {
		LOGF_WARN("%s: Handshake failed: got %02x %02x %02x %02x after second set", getAxisName(), rx[5*3+1], rx[5*3+2], rx[5*3+3], rx[5*3+4]);
		return false;
	}
	if(rx[5*4+1]!=tx[5*2+1] || rx[5*4+2]!=tx[5*2+2] || rx[5*4+3]!=tx[5*2+3] || rx[5*4+4]!=tx[5*2+4] ) {
		LOGF_WARN("%s: Handshake failed: got %02x %02x %02x %02x after second get", getAxisName(), rx[5*4+1], rx[5*4+2], rx[5*4+3], rx[5*4+4]);
		return false;
	}

	LOGF_INFO("%s: Handshake successful", getAxisName());
	return true;
}


bool Stepper::Init() {
	// Stop device, just in case it was left running
	if(!stop())
		return false;
	usleep(100*1000l);

	// Clear reset, undervoltage and driver error flags if present
	if(!setGStat(0x07))
		return false;

	// Setup Diagnosis 0 output to provide interrupts based on ramp function
	//
	if(!setDiag0EnableError(0))
		return false;
	if(!setDiag0EnableTemp(0))
		return false;
	if(!setDiag0EnableInterruptStep(0))
		return false;
	if(!setDiag0PushPull(1))
		return false;

	isrInit();

	// Set motor current parameters
	//
	if(!setRunCurrent(800))
		return false;
	if(!setHoldCurrent(800)) // Hold current = run current for StealthChop configuration
		return false;
	if(!setIHoldDelay(10))
		return false;
	if(!setTPowerDown(10))
		return false;

	if(!setInvertMotor(0)) 		// FIXME: should come from stored config data
		return false;

	if(!setRegister(TMCR_SW_MODE, 0))  // Disable all switches and StallGuard for now
		return false;

	// Set a default ramp (used in auto-tuning)
	//
	if(!setVStart(10))
		return false;
	if(!setA1(11250))
		return false;
	if(!setV1(200000))
		return false;
	if(!setAMax(7000))
		return false;
	if(!setVMax(100000))
		return false;
	if(!setMaxGoToSpeed(100000))
		return false;
	if(!setDMax(11250))
		return false;
	if(!setD1(7000))
		return false;
	if(!setVStop(10))
		return false;
	if(!setTZeroWait(100))
		return false;

	// Set PWM parameters for stealth chop
	//
	if(!setPWMFrequencyDivider(0))  // set PWM frequency divider to 0=2/1024 f_clk, i.e. 29 KHz at 15 MHz clock. Should be in 20/40 KHz range
		return false;
	if(!setPWMEnableStealthChop(1))
		return false;
	if(!setPWMAutoscale(1))         // stealth chop current regulator
		return false;
	if(!setPWMAutoGradient(1))      // stealth chop gradient regulator
		return false;

	// Set chopper parameters
	//
	if(!setChopperMode(0))          // If above the threshold, move to spread cycle mode
		return false;
	if(!setTPWMThreshold(0))        // Disable threshold to use only StealthChop during calibration
		return false;
	if(!setChopperMicroRes(0))      // full 256 microsteps for internal operation
		return false;
	if(!setChopperTOff(5))
		return false;
	if(!setChopperTBlank(2))
		return false;
	if(!setChopperHStart(4))
		return false;
	if(!setChopperHEnd(0))
		return false;

	LOGF_INFO("%s: Auto-tuning...", getAxisName());
	if(!chopperAutoTuneStealthChop(500, 5000))
		return false;

	// now that configuration is complete, set hold current to proper target 
	if(!setHoldCurrent(100)) 
		return false;

	if(debugLevel>=TMC_DEBUG_DEBUG)
		LOGF_DEBUG("%s: Successfully initialized", getAxisName());
	
	return true;
}


bool Stepper::close() {
	bool res1=stop();
	bool res2=TMC5160::close();
	return res1 && res2;
}
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

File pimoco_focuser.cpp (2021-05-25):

/*
    PiMoCo: Raspberry Pi Telescope Mount and Focuser Control
    Copyright (C) 2021 Markus Noga

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
    You should have received a copy of the GNU General Public License
    along with this program.  If not, see <https://www.gnu.org/licenses/>.
*/


#include "pimoco_focuser.h"
#include <libindi/indilogger.h>

#define CDRIVER_VERSION_MAJOR	1
#define CDRIVER_VERSION_MINOR	0


// Singleton instance
PimocoFocuser focuser;

// C function interface redirecting to singleton
//
extern "C" {

void ISGetProperties(const char *dev) {
	focuser.ISGetProperties(dev);
}

void ISNewBLOB(const char *dev, const char *name, int sizes[], int blobsizes[], char *blobs[], char *formats[], char *names[], int n) {
	focuser.ISNewBLOB(dev, name, sizes, blobsizes, blobs, formats, names, n);
}

void ISNewNumber(const char *dev, const char *name, double values[], char *names[], int n) {
	focuser.ISNewNumber(dev, name, values, names, n);
}

void ISNewSwitch(const char *dev, const char *name, ISState *states, char *names[], int n) {
	focuser.ISNewSwitch(dev, name, states, names, n);
}

void ISNewText(const char *dev, const char *name, char *texts[], char *names[], int n) {
	focuser.ISNewText(dev, name, texts, names, n);
}

void ISSnoopDevice(XMLEle *root) {
	focuser.ISSnoopDevice(root);
}

} // extern "C"


// Public class members
//

PimocoFocuser::PimocoFocuser() : stepper(getDeviceName(), "Focuser", FOCUSER_DIAG0_PIN), spiDeviceFilename("/dev/spidev0.2") {
	setVersion(CDRIVER_VERSION_MAJOR, CDRIVER_VERSION_MINOR);
    FI::SetCapability(FOCUSER_CAN_ABS_MOVE | FOCUSER_CAN_REL_MOVE | FOCUSER_CAN_ABORT | 
    	              // FOCUSER_CAN_REVERSE  |        // superseded by stepper class controls which serve both mount and focuser 
    	              FOCUSER_CAN_SYNC |
    	              // | FOCUSER_HAS_VARIABLE_SPEED  // superseded by stepper class controls which serve both mount and focuser      
    	              0);	
	setSupportedConnections(CONNECTION_NONE);
}

PimocoFocuser::~PimocoFocuser() {
	stepper.stop();
}

const char *PimocoFocuser::getDefaultName() {
	return "Pimoco focuser";
}

bool PimocoFocuser::initProperties() {
	if(!INDI::Focuser::initProperties()) 
		return false;

	FocusMaxPosN[0].max=2000000000;
	IUUpdateMinMax(&FocusMaxPosNP);

	stepper.initProperties(MotorN, &MotorNP, MSwitchS, &MSwitchSP, RampN, &RampNP, 
						   "MOTOR", "Motor", "SWITCHES", "Switches", "RAMP", "Ramp", FOCUS_TAB);

	// load configuration data from file, as there is no device with own storage
	loadConfig(true, MotorNP.name);
	loadConfig(true, MSwitchSP.name);
	loadConfig(true, RampNP.name);

    addDebugControl();
    return true;
}

bool PimocoFocuser::updateProperties() {
	if(!INDI::Focuser::updateProperties())
		return false;

	if(!stepper.updateProperties(this, MotorN, &MotorNP, MSwitchS, &MSwitchSP, RampN, &RampNP))
		return false;

	if(isConnected()) {
		// ...
	} else {
		// ...
	}

	return true;
}

bool PimocoFocuser::ISNewBLOB(const char *dev, const char *name, int sizes[], int blobsizes[], char *blobs[], char *formats[], char *names[], int n) {
	if(dev==NULL || strcmp(dev,getDeviceName()))
    	return INDI::Focuser::ISNewBLOB(dev, name, sizes, blobsizes, blobs, formats, names, n);

    // if(strcmp(name, ...)) { } else

	return INDI::Focuser::ISNewBLOB(dev, name, sizes, blobsizes, blobs, formats, names, n);
}

bool PimocoFocuser::ISUpdateNumber(INumberVectorProperty *NP, double values[], char *names[], int n, bool res) 
{
	if(res) {
		IUUpdateNumber(NP, values, names, n);               
		saveConfig(true, NP->name);
	}
	NP->s=res ? IPS_OK : IPS_ALERT;
	IDSetNumber(NP, NULL);
	return res;
}

bool PimocoFocuser::ISNewNumber(const char *dev, const char *name, double values[], char *names[], int n) {
	if(dev==NULL || strcmp(dev,getDeviceName()))
		return INDI::Focuser::ISNewNumber(dev, name, values, names, n);

	int res;
	if((res=stepper.ISNewNumber(&MotorNP, &RampNP, name, values, names, n)) > 0) {
		saveConfig(true, MotorNP.name);
		saveConfig(true, RampNP.name);
		return true;
	} else if(res==0)
		return false;
   
	return INDI::Focuser::ISNewNumber(dev, name, values, names, n);
}

bool PimocoFocuser::ISNewSwitch(const char *dev, const char *name, ISState *states, char *names[], int n) {
	if(dev==NULL || strcmp(dev,getDeviceName()))
		return INDI::Focuser::ISNewSwitch(dev, name, states, names, n);

	int res;
	if((res=stepper.ISNewSwitch(&MSwitchSP, name, states, names, n)) >0) {
		saveConfig(true, MSwitchSP.name);
		return true;
	} else if(res==0)
		return false;

	return INDI::Focuser::ISNewSwitch(dev, name, states, names, n);
}

bool PimocoFocuser::ISNewText(const char *dev, const char *name, char *texts[], char *names[], int n) {
	if(dev==NULL || strcmp(dev,getDeviceName()))
		return INDI::Focuser::ISNewText(dev, name, texts, names, n);

    // if(strcmp(name, ...)) { } else

	return INDI::Focuser::ISNewText(dev, name, texts, names, n);
}

bool PimocoFocuser::ISSnoopDevice(XMLEle *root) {
	return INDI::Focuser::ISSnoopDevice(root);
}

bool PimocoFocuser::saveConfigItems(FILE *fp){
    INDI::Focuser::saveConfigItems(fp);

    IUSaveConfigNumber(fp, &MotorNP);
    IUSaveConfigSwitch(fp, &MSwitchSP);
    IUSaveConfigNumber(fp, &RampNP);

    return true;
}

// Protected class members
//

bool PimocoFocuser::Connect() {
	LOGF_INFO("Attempting connection on %s", spiDeviceFilename);
	if(!stepper.open(spiDeviceFilename)) {
		LOGF_WARN("Connection on %s failed", spiDeviceFilename);
		return false;
	}
	if(!ReadFocuserStatus())
		return false;
	LOGF_INFO("Connection on %s successful", spiDeviceFilename);

	uint32_t pp=getPollingPeriod();
	if (pp > 0)
		SetTimer(pp);

	return true;
}

bool PimocoFocuser::Disconnect() {
	if(!stepper.close()) {
		LOG_WARN("Error closing connection");
		return false;
	}
	LOG_INFO("Successfully closed connection");
	return true;
}

bool PimocoFocuser::Handshake() {
	return true;
}

void PimocoFocuser::TimerHit() {
	if(!isConnected())
		return;

	ReadFocuserStatus();

    SetTimer(getCurrentPollingPeriod());
}


bool PimocoFocuser::ReadFocuserStatus() {
	auto pos=0;
	if(!stepper.getPosition(&pos)) {
		LOG_ERROR("Error reading position");
	    FocusAbsPosNP.s = IPS_ALERT;
	    return false;
	} else {
	    auto status=stepper.getStatus();
	    if((FocusAbsPosNP.s==IPS_BUSY) && (status&Stepper::TMC_STAND_STILL))
	    	LOGF_INFO("Focuser has reached position %u", pos);

	    FocusAbsPosN[0].value = pos;
	    FocusAbsPosNP.s = (status & Stepper::TMC_STAND_STILL) ? IPS_OK : IPS_BUSY;
	    FocusRelPosNP.s = FocusAbsPosNP.s;
	    IDSetNumber(&FocusAbsPosNP, NULL);		
	    IDSetNumber(&FocusRelPosNP, NULL);		
	}
	return true;
}


IPState PimocoFocuser::MoveAbsFocuser(uint32_t targetTicks) {
	if(!stepper.setTargetPosition(targetTicks)) {
		LOG_ERROR("Error setting focuser target position");
		return IPS_ALERT;
	}
	return IPS_BUSY;
}
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

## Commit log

2021-03-23 compiles but doesn't communicate with device yet
    [main.cpp, pimoco_tmc5160.cpp, pimoco_tmc5160.h]
2021-03-24 first version which communicates with Trinamic, doesn't yet move the motor
    [main.cpp, pimoco_tmc5160.cpp, pimoco_tmc5160.h]
2021-03-24 implemented syncing of current position, caching of write-only register values in driver for convenience, and structured logging
2021-03-24 added curent calculations from/to mA, improved use of system timer for blocking GoTos.
2021-03-24 factored out SPI communication in base class
2021-03-24 factored out basic device register functions in separate class
2021-03-24 factored out higher functions into stepper subclass
2021-03-24 using refactored stepper class
2021-03-29 close #1: first working version of the driver which can initialize and execute gotos on each of the three motors
2021-03-29 improved motor settings and added first RA hour and sidereal rate calculations
2021-03-31 towards #2: first indi focuser driver which compiles, still need to sort out the connection
2021-04-03 towards #2: first working device connection
2021-04-03 close #2: first working indi focuser driver
2021-04-04 towards #7: added hold/run current controls
2021-04-04 close #14: changed implementation of stop() to use goto(current_position)
2021-04-05 close #15: refactored to use INDI logger methods in stepper-related classes
2021-04-05 towards #3: first mount class which compiles, runs, and initializes steppers
2021-04-05 towards #3: factored out stepper Indi UI code into stepper cllass
2021-04-06 added libnova for mount calculations
2021-04-06 factored out reversal of axis direction into stepper class
    [pimoco_focuser.cpp]
2021-04-06 factored out reversal of axis direction into stepper class, added first RA calculations with libnova
    [pimoco_mount.cpp]
2021-04-06 factored out reversal of axis direction into stepper class, added steps/rev and gear ratio properties and calculation of angular positions
    [pimoco_stepper.cpp]
2021-04-06 added property for motor clock in hz
2021-04-07 fixed error handling for focuser Connect()
    [pimoco_focuser.cpp]
2021-04-08 close #21: added mount slewing commands MoveNS, MoveWE and SetSlewRate
2021-04-08 close #27: added XML files for Indi driver installation
2021-04-09 #18: added wiringPi library for interrupt handling
2021-04-09 #18: added connections to diag0 interrupt pins
2021-04-09 To #18: added diag0 pin
2021-04-09 To #18: first interrupt support which catches and resets interrupts; no other actions yet
    [pimoco_tmc5160.cpp, pimoco_tmc5160.h]
2021-04-24 isr fix & logging improvement
    [pimoco_stepper.cpp, pimoco_tmc5160.cpp, pimoco_tmc5160.h]
2021-04-24 RasPi 4 WiringPi fix
2021-04-26 made getters/setters public for use in mount class
2021-04-28 #17: added basic properties for stallguard, fast chopper moes
    [pimoco_stepper.cpp, pimoco_tmc5160.h]
2021-04-28 fixed park handling, deactivating guider motion on slew/goto/park
    [pimoco_mount.cpp]
2021-04-28 close #17: enhanced motor controll with DCStep, StallGuard etc.
    [pimoco_stepper.cpp, pimoco_tmc5160.h]
2021-05-02 factored out more mount capabilities into individual files
2021-05-02 #23: first working mount limits for min/max altitude
2021-05-03 #24: first meridian flip code
    [pimoco_mount.cpp, pimoco_mount_goto.cpp, pimoco_mount_limits.cpp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]
2021-05-04 replaced libnova calls with corresponding indi calls
    [pimoco_mount.cpp]
2021-05-04 brought default park position in line with german eq mounts to HA -6h, Dec 90°
2021-05-04 #24: can trigger meridian flip by clicking pier side buttons, fixed HA limit defaults
    [pimoco_mount_ui.cpp]
2021-05-04 #24: fixes towards meridian flip
    [pimoco_mount_goto.cpp, pimoco_mount_limits.cpp]
2021-05-05 moved materials into wiki
2021-05-09 #24: goto to current coordinates now triggers meridian flip
    [pimoco_mount_goto.cpp]
2021-05-09 #23: better logging for mount limits
2021-05-13 #32: switched to SPI mode 3 at 4.5 MHz
2021-05-24 #32: added dtoverlay files for spi0-3cs and spi-4cs
2021-05-24 #32: new wirings for DIAG0 pins compatible with mode 3 on spi0-4cs
2021-05-24 #32: move to single SPI ioctl with array of transfers
2021-05-25 #32: added HA goto accuracy threshold to avoid endless chase conditions at low speed
    [pimoco_mount_timer.cpp]
2021-05-25 moved to physical pin numbers for interrupts
2021-05-25 setup now uses interrupts, to detect wiring errors
    [pimoco_stepper.cpp]
2021-05-31 #11: added first 2-layer PCB
    [pimoco-B_Cu.gbl, pimoco-B_Mask.gbs, pimoco-B_SilkS.gbo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]
2021-06-03 close #42: added sync button for custom rate tracking
2021-06-08 #41: moved to physical side of pier reporting, fixed automatic meridian flip
    [pimoco_mount_goto.cpp, pimoco_mount_limits.cpp, pimoco_mount_timer.cpp]
2021-06-14 added missing return value
    [pimoco_mount_track.cpp]
2021-06-14 close #41: fixed HA mount limits to deal with edge case close to meridian
    [pimoco_mount_goto.cpp, pimoco_mount_limits.cpp, pimoco_mount_timer.cpp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]
2021-06-15 #38, #43: made device & horizon coordinates & time explicit properties and updated limit checks accordingly
2021-07-04 close #11: added PCB image

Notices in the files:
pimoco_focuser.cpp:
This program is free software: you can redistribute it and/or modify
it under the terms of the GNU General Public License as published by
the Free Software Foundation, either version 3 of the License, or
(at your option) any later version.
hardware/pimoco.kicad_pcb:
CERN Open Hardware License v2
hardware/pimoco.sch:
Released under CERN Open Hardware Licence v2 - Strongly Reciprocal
